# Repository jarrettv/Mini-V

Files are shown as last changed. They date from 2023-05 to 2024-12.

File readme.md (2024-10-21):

# Mini-V

Mini-V is a compact core-xy printer with a build volume of 180mm³ using 2020 extrusions. The printer is designed to maximize print volume with a minimal footprint.

_October 2024 Update: We gathered a ton of great feedback from the Mini-V Group Build in Reno at VICE 2024. We have multiple builders sending in tips and feedback. We also now have full assembly CAD and a build guide available. Enjoy!_

<p align="center">
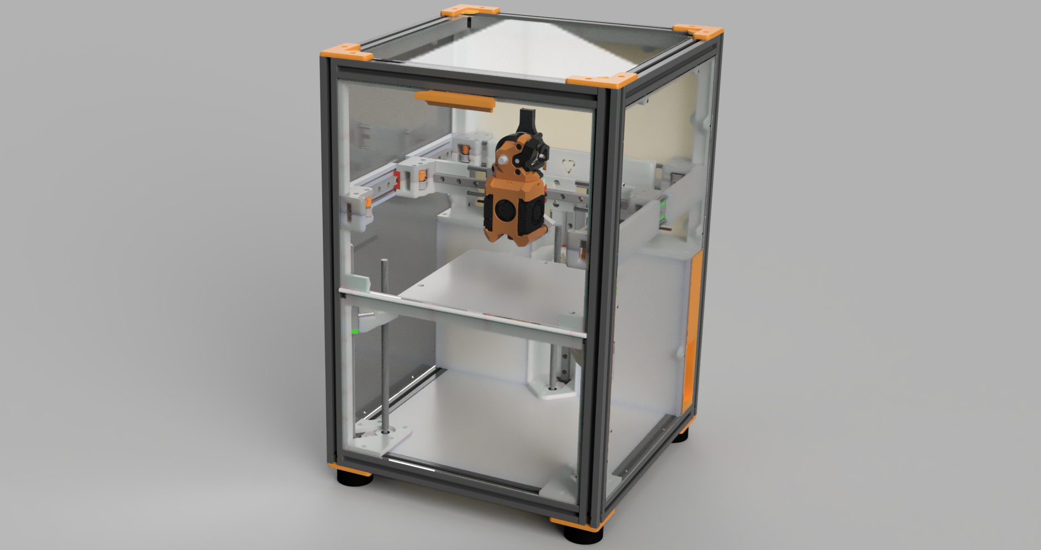
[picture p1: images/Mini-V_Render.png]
  
</p>

- Easy to build 2020 box design ✅
- Super light carbon fiber rod backed X rail ✅
- Sleek flush panels enclosure ✅
- Quick access electronics and host ports ✅
- Fold-down door and easy to remove top panel ✅
- Consistently perfect first layers with Boop ✅
- Automatic bed leveling ✅
- Easy belt tensioning knobs ✅
- Hi-temp dual-mag tri-mount stay-put kinematic bed 😅 ✅
- Magnetic toolhead with dual 4010 part cooling ✅
- Extra headroom for umbilical/PTFE tube ✅
- Dedicated high-voltage and low-voltage areas ✅
- No drag chains ✅
- Mostly M3 SHCS and easy to source hardware ✅
- Toolchanger ready! ↔️

Prototype build log on Discord here: #"jv's Mini-V a custom compact 180³ build using 2020 and CF rods"

- [Specs](./docs/Specs.md) for detailed specifications
- [BOM](./docs/BOM.md) for bill of materials
- [Printing Parts](./docs/PrintingParts.md) for slicer settings and print tips
- [Build Guide](./docs/BuildGuide.md) for step-by-step build instructions
- [Startup Config](./docs/StartupConfig.md) for Klipper configuration and startup routine
- [RepRap History](./docs/RepRapHistory.md) for how this open source printer evolved
- [TODO](./docs/TODO.md) for remaining design areas

## Community Design

Custom magnetic Yavoth toolhead mod with integrated PZ board mount:

<p align="center">
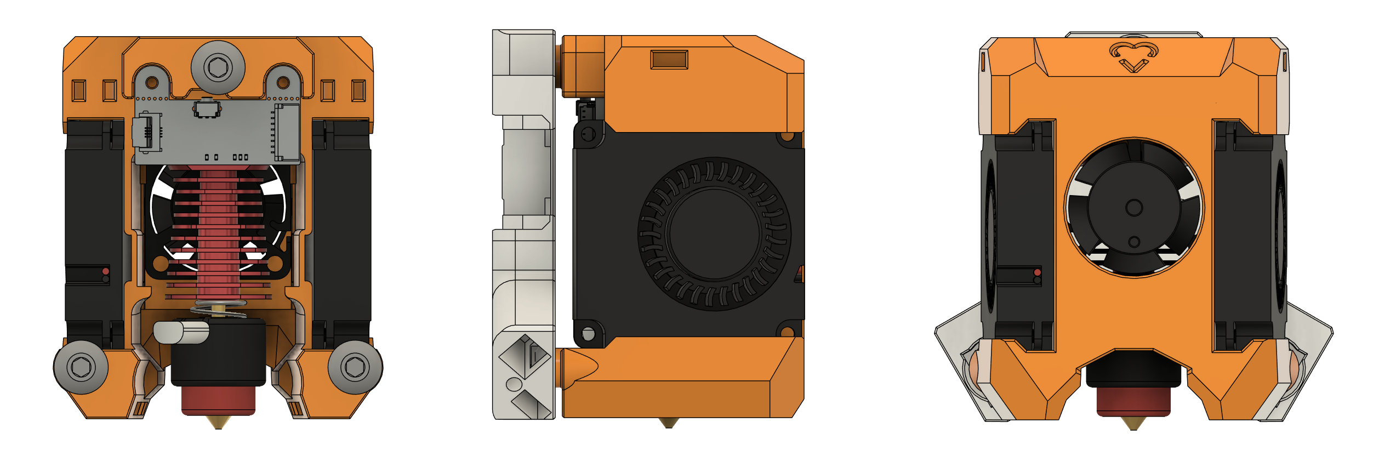
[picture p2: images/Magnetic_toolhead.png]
  
</p>

Although Mini-V is almost a completely custom design, it does utilize the following community designs:

- [Yavoth Toolhead](https://github.com/chirpy2605/voron) by `chirpy2605`
- [Belt Clips](https://github.com/zruncho3d/vampire_bat) by `zruncho3d`
- Inspiration from Voron Trident and is derived from Tiny-T frame dimensions

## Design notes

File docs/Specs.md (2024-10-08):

# Specifications

|  Spec | Desc |
| --- | --- |
| Print Size | 180mm³ ♦️|
| Kinematics | Core-XY |
| Extrusions | 2020 |
| Structure | 5mm Rods |
| Enclosure | Yes, flush |
| Door | Fold-down |
| Bed Leveling | 3-point Automatic |
| Z Accuracy | 0.1µm within a range of 6µm |
| Z Motion | Integrated lead-screws |
| A/B Voltage | 24v or 48v 🔰 |
| A/B Size | NEMA 17 |
| Belts | 2MGT (GT3) |
| Toolhead Board | EBB36 |
| Mainboard | E3EZ |
| Host CPU | Pi CM4 |
| Extruder | G2 |
| Hotend Cooling | 25x10 Axial |
| Part Cooling | Dual 40x10 Blowers |
| Hardware | M3 SHCS 98% |
| Nozzle | High-flow |
| Bed Heater | 300W 120V |
| Rear-clearance | Minimal, angled mains plug |
| Speed Benchy | Very fast |

♦️ Note: all specs are for the default build. Although 180mm build height is possible, with V0 integrated lead screw motors, we will target 170mm.

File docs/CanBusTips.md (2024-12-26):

Please see https://canbus.esoterical.online/

python3 ~/katapult/scripts/flashtool.py -f ~/klipper/out/klipper.bin -d /dev/serial/by-id/usb-katapult_stm32g0b1xx_4A00290012504B4B38383620-if00

mainboard: 183fbc1d936f

provoke3d adxl ampon
make flash FLASH_DEVICE=0483:df11

8d010481812b

python3 ~/katapult/scripts/flashtool.py -i can0 -u 8d010481812b -f ~/klipper/out/klipper.bin

usb-katapult_stm32g0b1xx_4A00290012504B4B38383620-if00

python3 ~/katapult/scripts/flashtool.py -f ~/klipper/out/klipper.bin -d /dev/serial/by-id/usb-katapult_stm32g0b1xx_4A00290012504B4B38383620-if00

21183091201e

python3 ~/katapult/scripts/flashtool.py -i can0 -u 21183091201e -f ~/klipper/out/klipper.bin

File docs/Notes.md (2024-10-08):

Leave deck panel off until back ebays are setup
Belts, start in the rear corner, leave XY inner idler off
  run belts all the way and insert XY inner idler after belts run, turn printer upside down if screws enter from below

When putting on lead screw nuts, move all the way to bottom of z rail before you tighten them down

Y-rail carriages may rub on steel rods, need to add some tolerance for various MGN-9H carriages ✅

Make the foot spacers 2mm taller to account for different brands lead-screw steppers ✅

Move the Z1 bottom motor mount screws to outside so they are more easily accessible for adjustments

Add notches into front Z motor mounts so front feet screws don't interfere  ✅

Add tiny slots to Z motor mounts so there is some play
  Shouldn't be necessary, need more testing results

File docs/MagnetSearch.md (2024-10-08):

# Magnets

Mini-V uses magnets in high-temperature areas which means ordinary magnets are not up to the task. I have over a years worth of print time using <abbr title="Samarium Cobalt">SmCo</abbr>  magnets and they hold up great even with repeated high bed/chamber temp cycles.

Normal neodymium magnets fail after the first couple heat cycles. However, there are high-temp classes:

## Neodymium Temp Classifications
- N	176°F (80°C)	590°F (310°C)
- NM	212°F (100°C)	644°F (340°C)
- NH	248°F (120°C)	644°F (340°C)
- NSH	302°F (150°C)	644°F (340°C) **➡️ These and below would work**
- NUH	356°F (180°C)	662°F (350°C)
- NEH	392°F (200°C)	662°F (350°C)
- NAH	428°F (220°C)	662°F (350°C)

## Bed Magnets

The bed magnets need to hold the bed firmly for the following activities:
* Heating bed to ~110°C for printing
* Pulling off the spring steel sheet
* Moving or turning the printer upside down

### Target dimensions
- 20 mm = .787 inches 3/4
- 10 mm = .4 inches 1/2
- 5 mm = .2 inches 1/8

### Candidates

* 20x10x5mm SmCo Magnets (Found on Ali)
  * No longer available
  * Great size and work fantastic
  * See [bed_Mag_Kinematic_Mount_x3.stl](../parts/bed_Mag_Kinematic_Mount_x3.stl)

* High Temp N42SH Neodymium Magnets 1 in x 1/2 in x 1/4 in Rare Earth Block
  * Oversized but very strong pull
  * See [bed_[a]_Kinematic_Bed_Mount_Neo_SH_Large_x3.stl](../parts/bed_[a]_Kinematic_Bed_Mount_Neo_SH_Large_x3.stl)

* SmCo Magnets 1/2 in x 1/2 in x 1/4 in Samarium Cobalt Block
  * Workable, but doesn't quite seem strong enough
  * See [bed_[a]_Kinematic_Bed_Mount_SmCo_Small_x3.stl](../parts/bed_[a]_Kinematic_Bed_Mount_SmCo_Small_x3.stl)

## Toolhead Magnets

The toolhead magnets need to hold the toolhead firmly for the following activities:
* Printing up to ~270°C and up to 70°C chamber temps
* Sensorless homing
* Fast acceleration printing

### Candidates

* 1/2" x 1/4" x 1/8" Blocks - SmCo - Samarium Cobalt
  * Must double-up for stronger hold
  * See [gantry_X_Carriage_Magnetic_x1.stl](../parts/gantry_X_Carriage_Magnetic_x1.stl)

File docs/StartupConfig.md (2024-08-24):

# Startup and Configuration

Follow klipper docs
Follow Voron Trident docs

TBD Mini-V specific startup and config

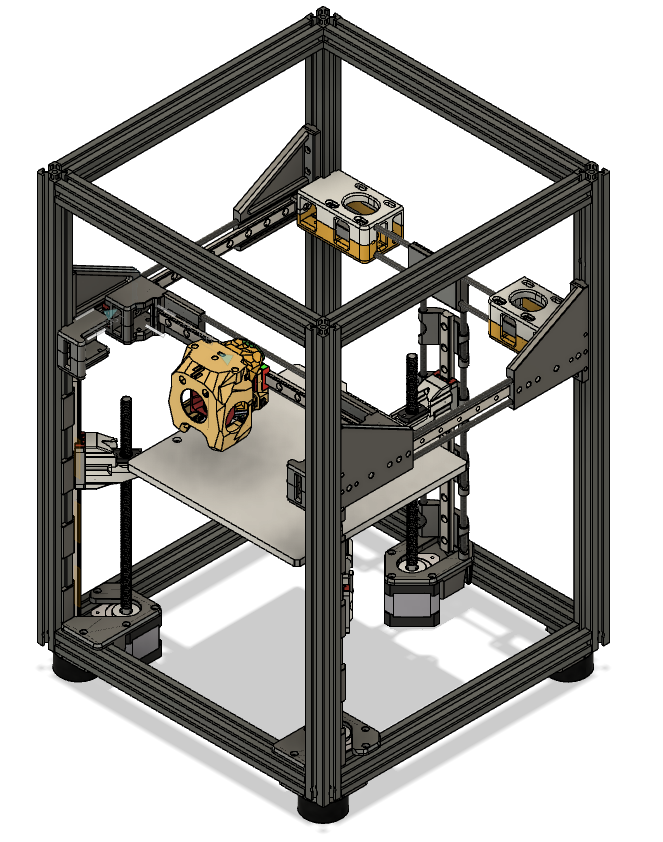
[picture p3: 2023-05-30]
images/concept.png

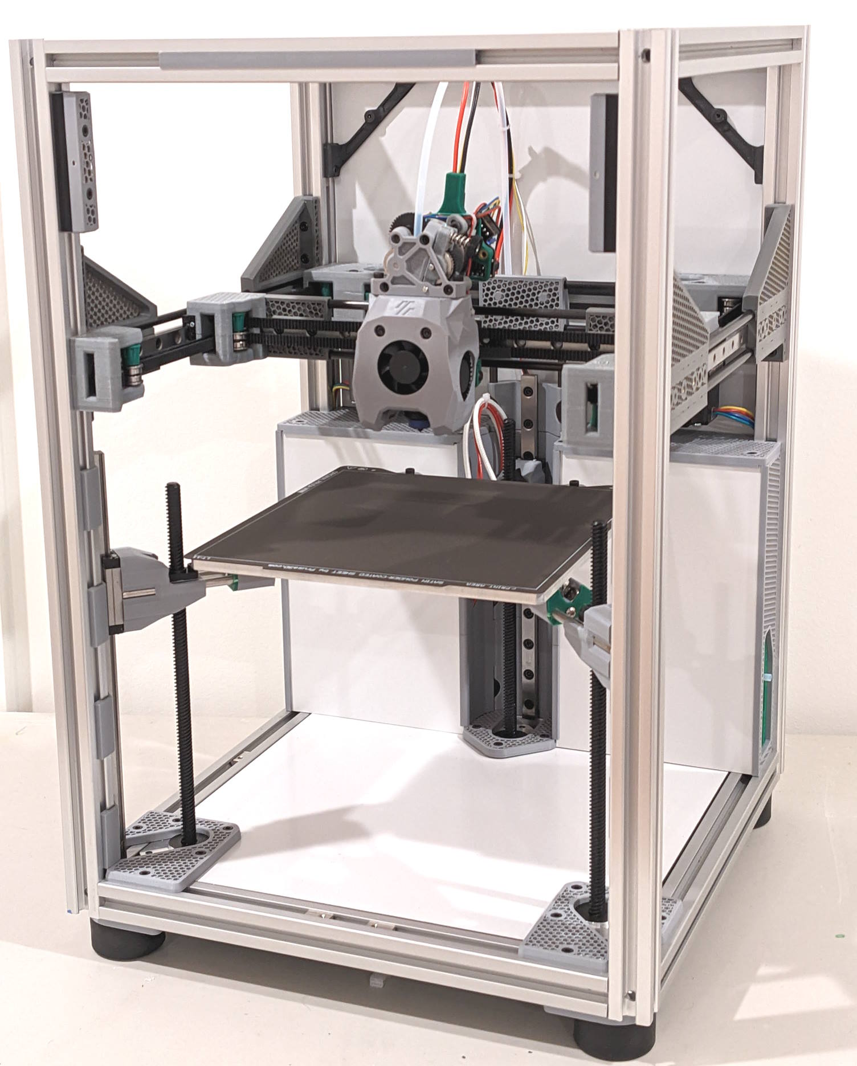
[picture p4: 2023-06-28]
images/Mini-V_prototype_june_2023.jpg

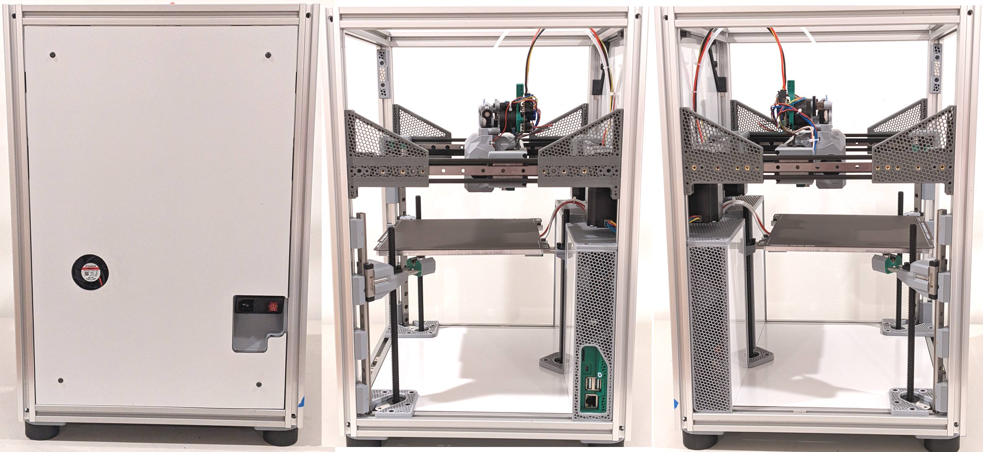
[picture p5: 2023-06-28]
images/Mini-V_back_right_left.jpg

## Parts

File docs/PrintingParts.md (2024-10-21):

# Printing Parts

## Main parts

Many of the main parts are structural so we recommend a filled filament. Although they were specifically designed to be printable with an 0.6mm nozzle, I still recommend a 0.4mm nozzle as the parts require less post-processing. 

| Setting | Value |
| --- | --- |
| Nozzle | 0.6mm or 0.4mm |
| Filament | CF or GF ABS or ASA |
| Infill | 25% (honeycomb) |
| Extrusion width | 0.6mm or 0.4mm |
| Perimeters | 4 |
| Top layers | 5 |
| Bottom layers | 4 |

- [x] bed_Front_Z_Rail_Mount_x4
- [x] bed_Front_Z_Rail_Panel_A_Mount_x2
- [x] bed_Front_Z_Rail_Panel_B_Mount_x2
- [ ] bed_Mag_Kinematic_Mount_x3
- [x] bed_Z0_Motor_Mount_x1
- [x] bed_Z1_Motor_Mount_Rear_x1
- [x] bed_Z1_Rail_Mount_Top_x1
- [x] bed_Z1_Rail_Mount_Wire_Manage_x1
- [x] bed_Z1_Rail_Mount_x3
- [x] bed_Z1_Top_Tensioner_Clamp_Back_x1
- [x] bed_Z1_Top_Tensioner_Clamp_Front_x1
- [x] bed_Z2_Motor_Mount_x1
- [x] bed_Z_Carriage_Mount_x3
- [x] ebay_E3EZ_Mount_x1
- [x] ebay_High_Voltage_Side_x1
- [x] ebay_Low_Voltage_Side_x1
- [x] ebay_Mains_Inlet_Mount_x1
- [ ] ebay_PSU_Mount_x2
- [x] ebay_Top_Cover_High_Voltage_x1
- [x] ebay_Top_Cover_Low_Voltage_x1
- [x] gantry_A_Motor_Mount_Bot_x1
- [x] gantry_A_Motor_Mount_Top_x1
- [x] gantry_A_Motor_Mount_x1
- [x] gantry_B_Motor_Mount_Bot_x1
- [x] gantry_B_Motor_Mount_Top_x1
- [x] gantry_B_Motor_Mount_x1
- [x] gantry_Front_Idler_Bot_Left_x1
- [x] gantry_Front_Idler_Bot_Right_x1
- [x] gantry_Front_Idler_Top_Left_x1
- [x] gantry_Front_Idler_Top_Right_x1
- [x] gantry_XY_Joint_Left_Bot_x1
- [x] gantry_XY_Joint_Left_Top_x1
- [x] gantry_XY_Joint_Right_Bot_x1
- [x] gantry_XY_Joint_Right_Top_x1
- [x] gantry_X_Carriage_Magnetic_x1
- [x] gantry_X_Rail_End_Mount_x2
- [x] gantry_X_Rail_Mid_Mount_x2
- [x] gantry_Y_Rail_Mount_x4
- [x] panels_Clip_Door_Hinge_Latch_Left_x1
- [x] panels_Clip_Door_Hinge_Latch_Right_x1
- [x] panels_Clip_Dual_Mount_Wire_Slot_Right_x1
- [x] panels_Clip_Dual_Mount_Wire_Slot_Left_x1
- [x] panels_Clip_Dual_Mount_x2
- [x] panels_Clip_LED_Stick_A_x2
- [x] panels_Clip_LED_Stick_B_x2
- [ ] panels_Clip_Long_x6
- [x] panels_Clip_Magnet_Door_Latch_Left_x1
- [x] panels_Clip_Magnet_Door_Latch_Right_x1
- [ ] panels_Clip_Short_x2
- [x] panels_Clip_Single_Mount_x8
- [x] panels_Clip_x31
- [x] panels_Front_Door_Bottom_Rest_x2
- [t] panels_Front_Door_Hinge_Lower_Edge_Left_x1
- [t] panels_Front_Door_Hinge_Lower_Edge_Right_x1
- [t] panels_Front_Door_Hinge_Lower_Mid_Left_x1
- [t] panels_Front_Door_Hinge_Lower_Mid_Right_x1
- [t] panels_Front_Door_Hinge_Mid_x3
- [t] panels_Front_Door_Hinge_Upper_Left_x1
- [t] panels_Front_Door_Hinge_Upper_Right_x1

## Panel Clips (feature less)

Any of the clips that don't have special features can be printed with 0.6 nozzle in vase mode for an even better snap-in feel. The following settings have been tested with ABS-GF, YMMV. Depending on your bed and toolhead size, you can print many in a batch using "Complete individual objects" setting.

| Setting | Value |
| --- | --- |
| Nozzle | 0.6mm |
| Filament | ABS or ASA GF |
| Infill | none |
| Extrusion width | 0.85mm forced width |
| Perimeters | 1 *Spiral vase mode |
| Top layers | 0 |
| Bottom layers | 0 |
| Elephant foot comp. | 0 |

- [x] panels_Clip_30mm_x10
- [x] panels_Clip_45mm_x6
- [x] panels_Clip_60mm_x12

## Accent parts

Most of these parts are designed for 0.4mm nozzle. Choose a bright color to make them "pop"! 

> [!CAUTION]
> Filled filaments are ok too but I suggest you print a few tolerance test prints for your bearing stacks.

| Setting | Value |
| --- | --- |
| Nozzle | 0.4mm |
| Filament | ABS or ASA (bright color) |
| Infill | 40% (honeycomb) |
| Extrusion width | 0.4mm |
| Perimeters | 4 |
| Top layers | 5 |
| Bottom layers | 4 |

- [ ] gantry_[a]_Bearing_Stack_Double_x2
- [ ] gantry_[a]_Bearing_Stack_Double_x2_(filled)
- [ ] gantry_[a]_Bearing_Stack_Single_x8
- [ ] gantry_[a]_Bearing_Stack_Single_x8_(filled)
- [ ] gantry_[a]_Bearing_Stack_Washer_x12
- [ ] gantry_[a]_Belt_Clip_x2
- [ ] gantry_[a]_Guidler_Spacer_x2
- [ ] gantry_[a]_Guidler_Washer_x2
- [ ] bed_[a]_Kinematic_Bed_Mount_Neo_SH_Large_x3
- [-] bed_[a]_Kinematic_Bed_Mount_SmCo_Small_x3
- [-] bed_[a]_Mag_Kinematic_Mount_Cover_x3
- [ ] bed_[a]_Z1_Top_Tensioner_Knob_x2
- [ ] ebay_[a]_E3EZ_IO_Shield_x1
- [t] ebay_[a]_Foot_Mount_(LDO)_x4
- [-] ebay_[a]_Foot_Mount_(taller)_x4
- [ ] ebay_[a]_PSU_LED_Mount_x2
- [ ] panels_[a]_Door_Magnetic_Handle_x1
- [t] panels_[a]_Top_Latch_Mount_x4
- [ ] panels_[a]_Top_Latch_Pick_x4
- [x] toolhead_Yavoth_Revo_PZ_Magnetic_Cowl_x1
- [-] toolhead_[a]_Dragon_Burner_V8_Mini-V_x1
- [x] toolhead_[a]_Yavoth_Magnetic_Cowl_x1

## Mesh parts

The parts look solid but you need to print them with your favorite breathable infill. I prefer honeycomb at 25%.

| Setting | Value |
| --- | --- |
| Nozzle | 0.4mm |
| Filament | ABS or ASA (bright color) |
| Infill | 25% (honeycomb) |
| Extrusion width | 0.4mm |
| Perimeters | 4 |
| Top layers | 0 for first 3mm |
| Bottom layers | 0 for first 3mm |

- [ ] ebay_[a]_High_Voltage_Mesh_x1
- [ ] ebay_[a]_Low_Voltage_Mesh_x1

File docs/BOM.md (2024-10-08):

| Quantity | Part | For | Sources |
| --- | --- | --- | --- |
| 4 | HFSB5-2020-440-LCP-RCP | Corners | Misumi, Dllpdf, Amazon (DIY) |
| 8 | HFSB5-2020-270-TPW | Tops/bottoms | Misumi, Dllpdf, Amazon (DIY) |
| 6 | MGN9 Linear Rail 220mm length | Motion | Fabreeko, Ali |
| 2 | GATES GT3 6mm open belt ~150cm | Motion | Filastruder |
| 4 | F623-RS Bearings | Motion | Filastruder |
| 24 | F695 Bearings | Motion | Filastruder |
| 2 | NEMA 17 stepper motors | A/B motors | SteppersOnline, LDO |
| 3 | NEMA 17 steppers w/ 200mm lead screw | Z motors | SteppersOnline, LDO |
| 3 | 5mm Ø Carbon Fiber Rod 280mm length | X-rail backer | Amazon, Ali |
| 1 | 5mm Ø Carbon Fiber Rod 269mm length | Door hinge | Amazon, Ali |
| 4 | 5mm Ø Steel Rod 269mm length | Y-rail backer | Amazon, Ali |
| 4 | 5mm Ø Steel Rod 279mm length | Rear backer | Amazon, Ali |
| 6 | 5mm Ø Steel Rod 80mm length | Z kinematics | Amazon, Ali |
| 3 | Steel balls 10mm M4 threaded (magnetic) | Z kinematics | Filastruder, Amazon, Ali |
| 6 | High-temp magnets 20x10x5mm (SaCo) | Z kinematics | Specialty, Ali |
| 3 | M4x10 low-profile SHCS | Z kinematics | McMaster, BoltDepot, Ali |
| 6 | M5 washers | Z kinematics | McMaster, BoltDepot, Ali |
| 6 | High-temp magnets 1x0.5x0.25in (Neo SH) | Z kinematics | Specialty, Ali |
| 6 | High-temp magnets 0.5x0.25x0.125in (SaCo) | Magnetic toolhead | Specialty, Ali |
| 1 | 180mm² or 185mm² MIC6 bed | Bed | Mandala Rose Works |
| 1 | 180mm² PEI flex build plate | Bed | Prusa, DFH, KB3D, Fabreeko, West3D |
| 1 | 150mm² 300w AC heating pad | Bed | KB3D, Fabreeko, DFH |
| 1 | Galileo2 recommended | Extruder | DFH, KB3D, Fabreeko, West3D, Ali |
| 1 | E3D Revo PZ High-flow recommended | Hotend | DFH, KB3D, Fabreeko, West3D, Ali |
| 2 | 4010 24V blower fan | Part cooling | DFH, Fabreeko, West3D, Ali |
| 1 | 2510 24V blower fan | Hotend cooling | Amazon, DFH, Fabreeko, West3D, Ali |
| 4 | Rubber amplifier feet | | Amazon, Ali |
| 1 | BTT E3EZ 5 stepper control board | Electronics | BIQU, Amazon, Ali |
| 1 | BTT EBB36 CAN toolhead board | Electronics | BIQU, Amazon, Ali |
| 3 | BTT EZ Driver EZ2209 (2 extra for 24v) | Electronics | BIQU, Amazon, Ali |
| 2 | BTT EZ Driver EZ5160 RGB (for 48v) | Electronics | BIQU, Amazon, Ali |
| 1 | SSR Relay | Electronics | Amazon, Ali |
| 2 | Daylight on a stick | Electronics | DFH, KB3D, Fabreeko, West3D |
| 2 | M4 OD, M3 ID 30mm long steel tubes | Belt clips | DFH, Amazon, McMaster, Ali |
| 2 | GT2 20T Pulley | Hardware | Amazon, Filastruder, DFH |
| 4 | M4 thumb screws | Hardware | McMaster, BoltDepot, Ali |
| 2 | M5x40 hex head bolts | Hardware | McMaster, BoltDepot, Ali |
| 2 | M5 nuts | Hardware | McMaster, BoltDepot, Ali |
| 17 | M5x16 BHCS | Hardware | McMaster, BoltDepot, Ali |
| 2 | M3x10 BHCS | Hardware | McMaster, BoltDepot, Ali |
| ~150 | M3x4x5 Heatset brass inserts | Hardware | McMaster, BoltDepot, Ali |
| 1 | 3mm Clear Top Panel 269x269 | Panels | Hardware store, Amazon, Plastic |
| 2 | 3mm Clear side Panel 399x269 | Panels | Hardware store, Amazon, Plastic |
| 1 | 3mm Clear Front Door Panel XXXx269 | Panels | Hardware store, Amazon, Plastic |
| 1 | 3mm Clear Front Bottom Panel XXXx269 | Panels | Hardware store, Amazon, Plastic |
| 1 | 3mm ACM Rear Panel 399x269 | Panels | Hardware store, Amazon, Plastic |
| 1 | 3mm ACM Deck Panel 269x269 | Panels | Hardware store, Amazon, Plastic |
| 2 | 3mm ACM Mid Panel 120x200 | Panels | Hardware store, Amazon, Plastic |

Mostly M3x6, M3x8, M3x10, M3x20, M3x30, M3x35 SHCS

TBD M3 SHCS counts
TBD M3 FHCS counts
TBD M5 BHCS counts
TBD wires / lengths

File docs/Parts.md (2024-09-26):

| Part | Wt. | Qty | Main | Accent |
|---|---|-----|---|---|
| bed_Z0/Z2_Motor_Mount | 16.0g  | 2 | 32.0g  | |
| bed_Z1_Motor_Mount | 18.5g  | 1 | 18.5g  | |
| gantry_Y_Rail_Mount | 18.0g  | 4 | 72.0g  | |
| gantry_Front_Idler_Top / Bot |  6.0g  | 4 | 24.0g  | |
| gantry_AB_Idler_Mount_Top / Bot |  8.0g  | 4 | 32.0g  | |
| gantry_AB_Motor_Mount | 14.0g  | 2 | 28.0g  | |
| bed_Top_Tensioner_Clamp_Back | 12.0g  | 1 | 12.0g  | |
| bed_Top_Tensioner_Clamp_Front |  8.5g  | 1 |  8.5g  | |
| gantry_XY_Joint_Top / Bot |  6.5g  | 4 | 26.0g  | |
| gantry_XY_Joint_X_Rail_Mount |  7.0g  | 2 | 14.0g  | |
| gantry_X_Rail_Mid_Mount |  5.5g  | 2 | 11.0g  | |
| bed_Front_Z_Rail_Mount |  4.0g  | 6 | 24.0g  | |
| bed_Front_Z_Rail_Panel_Low/Up_Mount |  4.0g  | 4 | 16.0g  | |
| ebay_High/Low_Voltage_Side | 25.0g  | 2 | 50.0g  | |
| ebay_Mains_Inlet_Mount | 28.0g  | 1 | 28.0g  | |

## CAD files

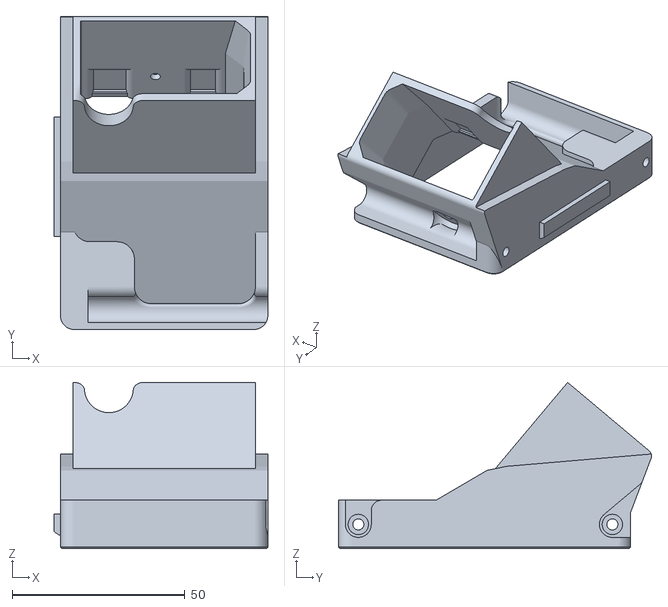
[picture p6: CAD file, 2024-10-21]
parts/ebay_Mains_Inlet_Mount_x1.stl
61.8 x 90.6 x 48.1

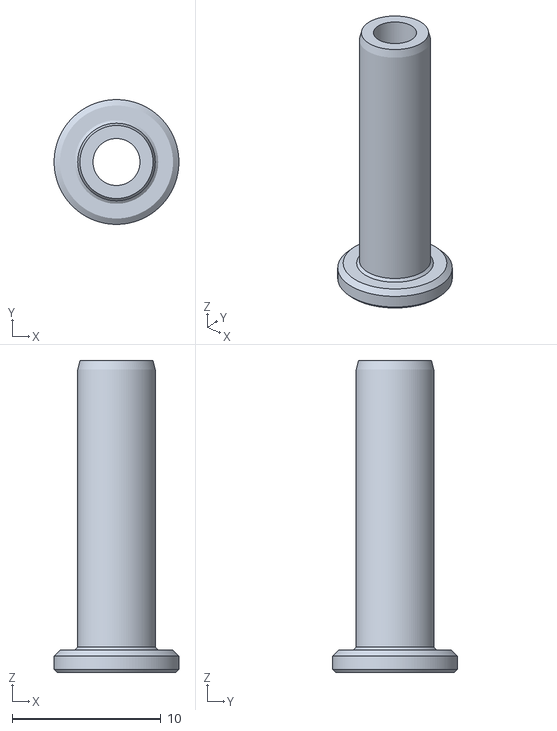
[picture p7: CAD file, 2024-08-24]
parts/gantry_[a]_Bearing_Stack_Full_x2.stl
8.40 x 8.40 x 21.0

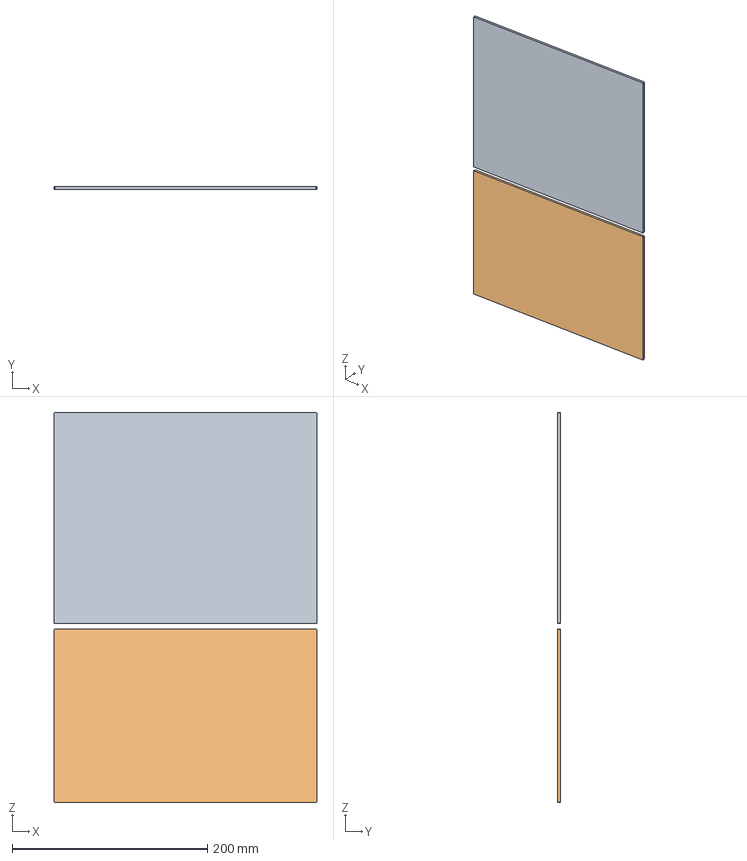
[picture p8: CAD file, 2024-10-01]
panels/Front_Door_Panels_Clear_v5.step
269.0 x 3.00 x 399.0 mm

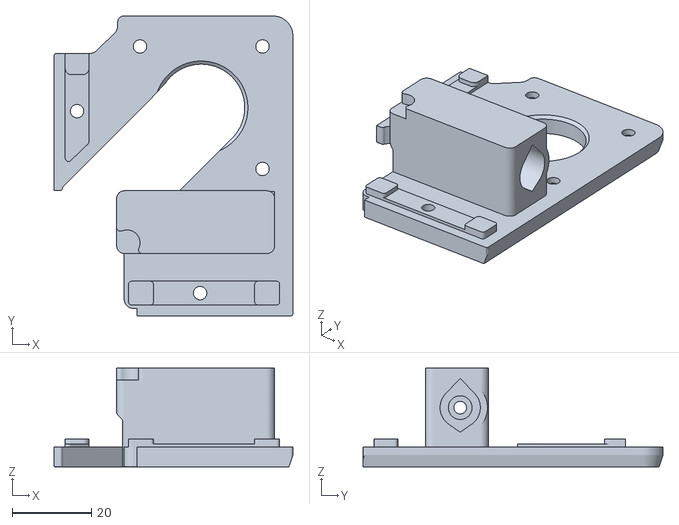
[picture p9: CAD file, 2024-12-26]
parts/bed_Z2_Motor_Mount_x1.stl
60.4 x 75.9 x 25.0

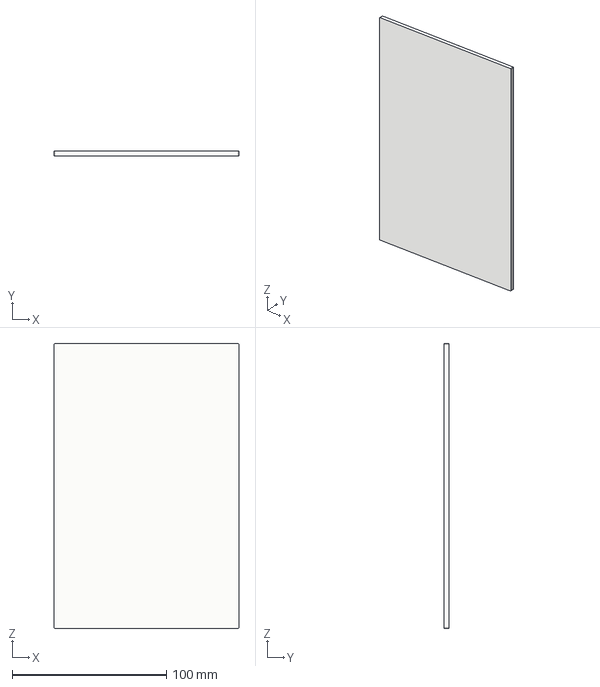
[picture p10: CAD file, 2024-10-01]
panels/Mid_Ebay_Panel_ACM_v2.step
120.0 x 3.00 x 185.0 mm

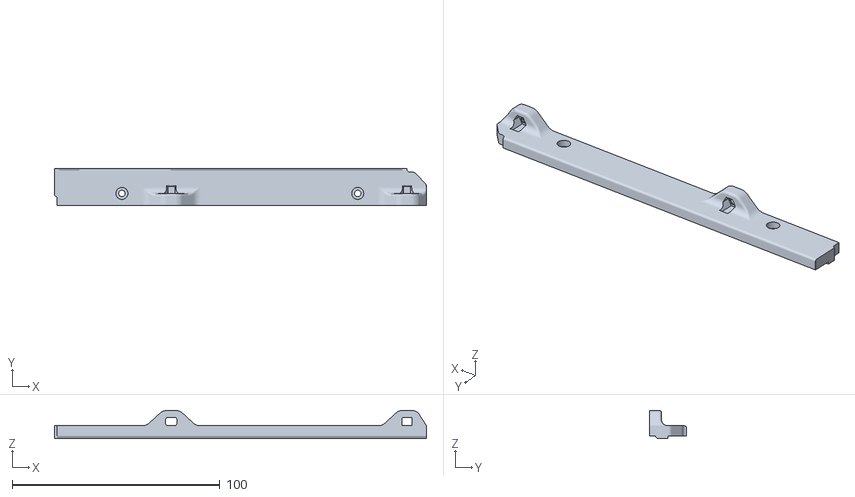
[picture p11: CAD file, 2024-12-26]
parts/panels_Side_Panel_Mag_Mount_Bot_Right_x1.stl
179.0 x 17.8 x 13.6

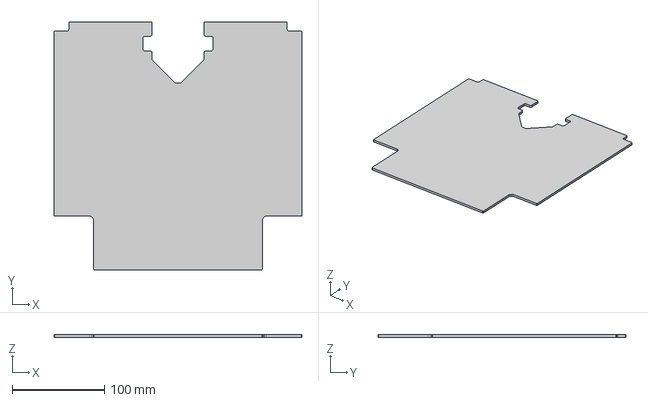
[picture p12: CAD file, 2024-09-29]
panels/Deck_Panel_ACM_v4.step
269.0 x 269.0 x 3.00 mm

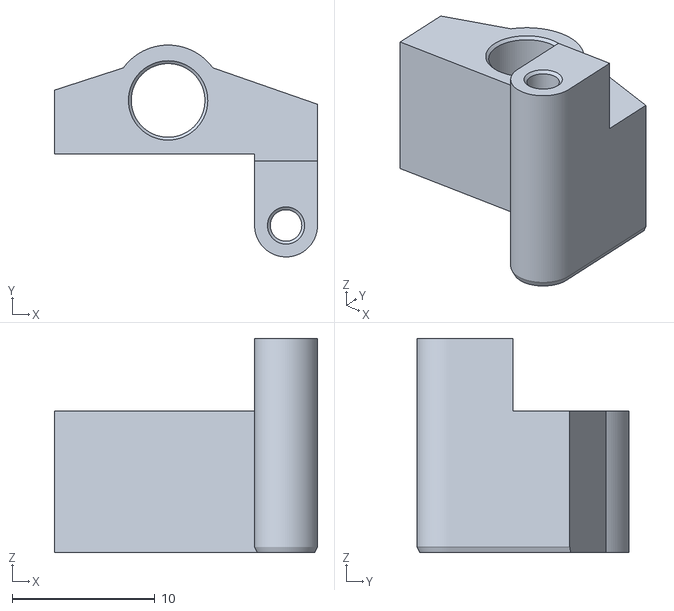
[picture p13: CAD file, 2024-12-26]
parts/panels_Front_Door_Hinge_Lower_Edge_Left_x1.stl
18.4 x 14.8 x 15.0

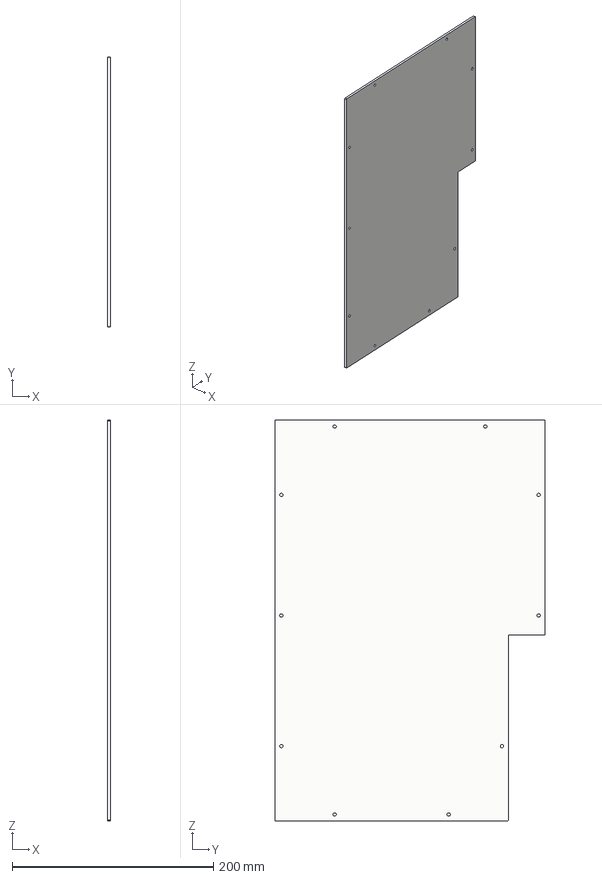
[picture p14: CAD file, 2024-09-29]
panels/Side_Panels_Clear_v3.step
3.00 x 269.0 x 399.0 mm

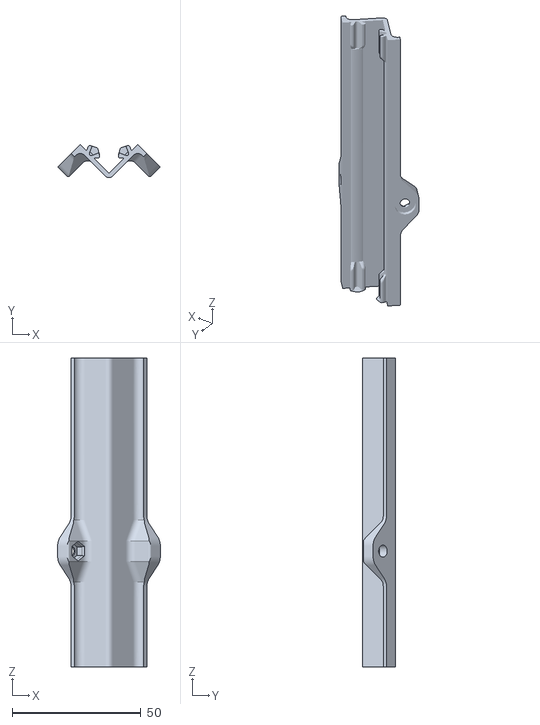
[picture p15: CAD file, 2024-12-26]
parts/panels_Clip_Upper_Rear_Left_x1.stl
39.9 x 13.0 x 120.0

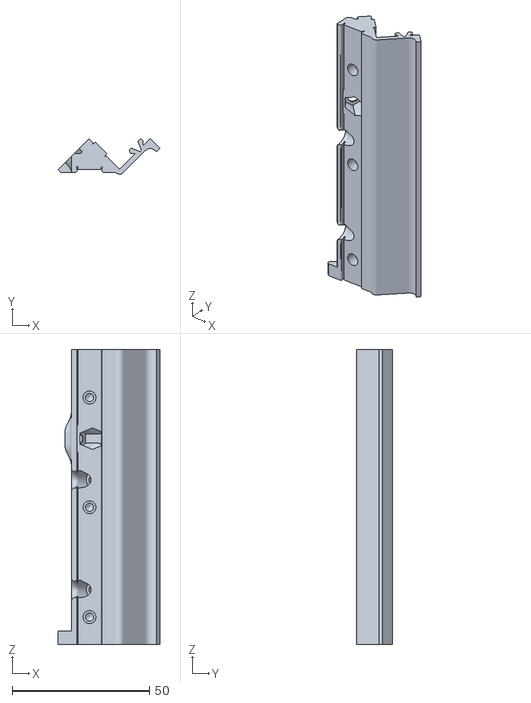
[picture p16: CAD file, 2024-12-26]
parts/bed_Front_Z_Rail_Mount_Right_Bot_x1.stl
37.1 x 13.0 x 107.5

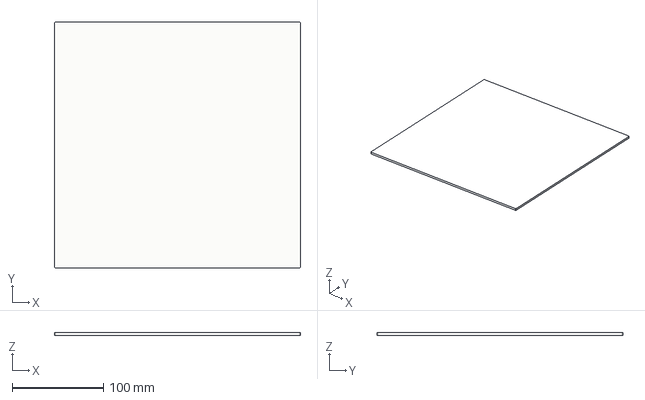
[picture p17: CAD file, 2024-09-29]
panels/Top_Panel_Clear_v1.step
269.0 x 269.0 x 3.00 mm

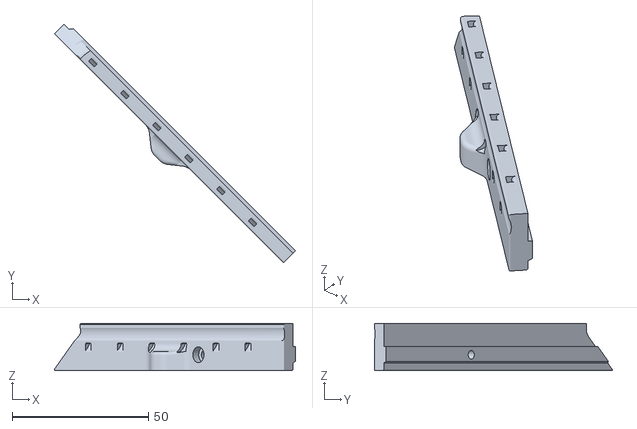
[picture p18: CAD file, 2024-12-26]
parts/panels_Rear_Panel_Bottom_Mount_Right_x1.stl
88.5 x 87.4 x 17.3

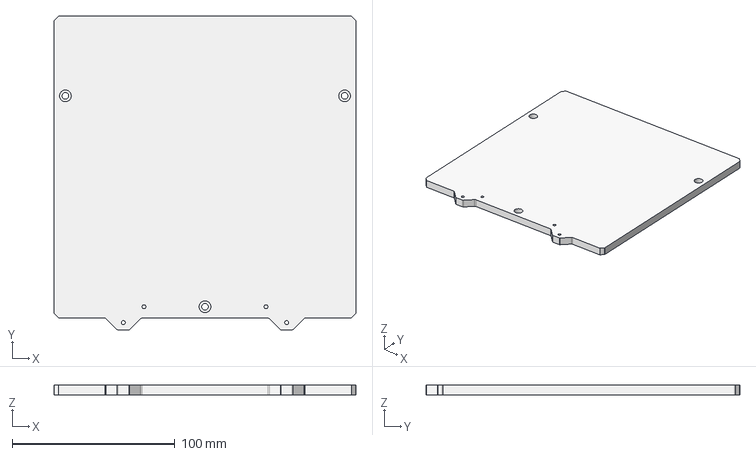
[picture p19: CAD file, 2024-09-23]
panels/185_Mini-V_MIC-6_Bed_v3.step
185.6 x 192.8 x 6.35 mm

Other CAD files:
panels/Back_Panel_ACM_or_Clear_v3.step
parts/panels_Clip_40mm_x6.stl
parts/panels_Clip_Upper_Rear_Right_x1.stl
parts/bed_Front_Z_Rail_Mount_Right_Top_x1.stl
panels/Deck_Panel_ACM_v1.step
parts/bed_Front_Z_Rail_Mount_Left_Bot_x1.stl
parts/bed_Front_Z_Rail_Mount_Left_Top_x1.stl
parts/bed_Front_Z_Rail_Mount_x4.stl
parts/bed_Front_Z_Rail_Panel_A_Mount_x2.stl
parts/bed_Front_Z_Rail_Panel_B_Mount_x2.stl
parts/bed_Mag_Kinematic_Mount_x3.stl
parts/bed_Z0_Motor_Mount_x1.stl
parts/bed_Z1_Motor_Mount_Rear_x1.stl
parts/bed_Z1_Rail_Mount_Bot_x1.stl
parts/bed_Z1_Rail_Mount_Top_x1.stl
parts/bed_Z1_Rail_Mount_Wire_Manage_x1.stl
parts/bed_Z1_Rail_Mount_x3.stl
parts/bed_Z1_Top_Tensioner_Clamp_Back_x1.stl
parts/bed_Z1_Top_Tensioner_Clamp_Front_x1.stl
parts/bed_Z_Carriage_Mount_x3.stl
parts/bed_[a]_Kinematic_Bed_Mount_Neo_SH_Large_x3.stl
parts/bed_[a]_Kinematic_Bed_Mount_SmCo_Small_x3.stl
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

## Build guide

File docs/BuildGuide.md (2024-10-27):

# Build Steps for Mini-V

> [!CAUTION]
> This build guide is a work-in-progress

## General Tips

- Use an ultra flat surface for assembly of frame
- Take a file or flattening stone to all mating surfaces, including all clips
- Panel clips should be snapped in diagonally towards the extrusion

## Gather Hardware

See [BOM](./docs/BOM) for Bill of Materials

## Print Parts

See [Printing Parts](./docs/PrintingParts)

## Heat Sets

- Grab some coffee, I hope you like putting in heat sets as there are many

> [!Tip]  
> You can build the left side of the printer, then the right side, or build them in parallel

## 🔁 Build left side

- Assemble 2 uprights and the bottom extrusion using blind joints M5x16 (2)
  - (optional) Bottom of bottom extrusion will need (2) T-nuts
  - You should have a U shape

<p align="center">
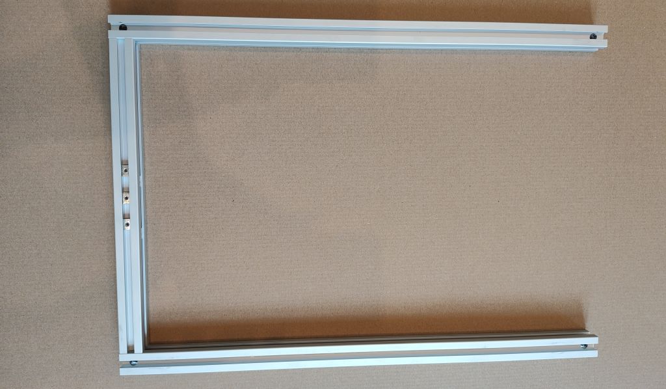
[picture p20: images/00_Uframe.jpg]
  
</p>

### Building Z0 axis

- Add the Z0 motor mount using a M3x30 (1) side and M3x8 (1) screw on top
  - Note: leave these screws slightly loose until the final frame tighten
- Loosely mount Z-rail clips using M3x10 (4)
  - Order from bottom up
    - bed_Front_Z_Rail_Mount, M3x10
    - panels_Clip
    - bed_Front_Z_Rail_Mount_B_Mount (lower), M3x10
    - panels_Clip
    - bed_Front_Z_Rail_Mount, M3x10
    - panels_Clip_Door_Hinge_Latch_Left, M3x8
    - bed_Front_Z_Rail_Mount_A_Mount (upper), M3x10

<p align="center">
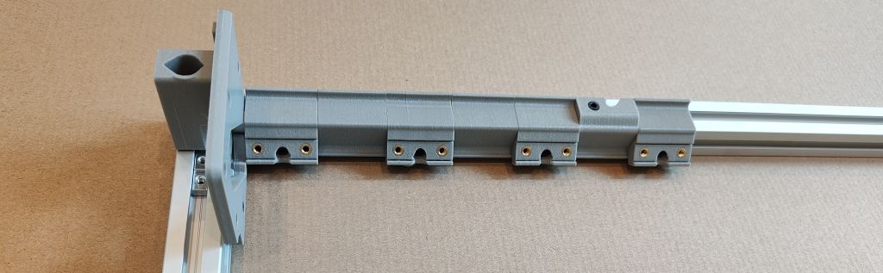
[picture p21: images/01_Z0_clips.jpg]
  
</p>

- Add the z-rail to clips using M3x6 (8)
  - Note: don't tighten down until all screws are in
  - Note: add your clip so carriage doesn't fall out when flipping upside down
- Tighten down Z-rail clips using ball end hex
  - Note: the top clip should line-up or you may need to adjust the clips

<p align="center">
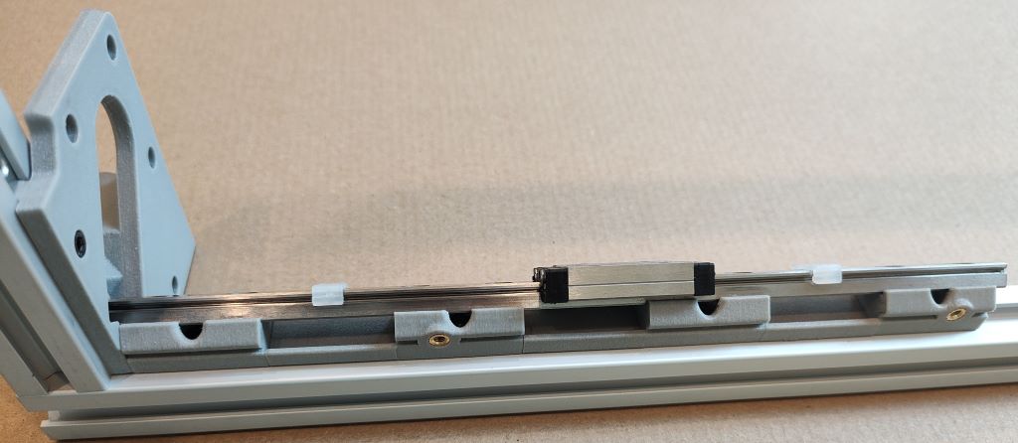
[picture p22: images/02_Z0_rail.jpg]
  
</p>

### Rear E-bay mount (low voltage)

- Note: leave these screws for the ebay mount loose until later, otherwise it might tweak the frame
- Add T-nuts to high-voltage ebay part using M3x10 (1) side middle and M3x6 (1) side top

<p align="center">
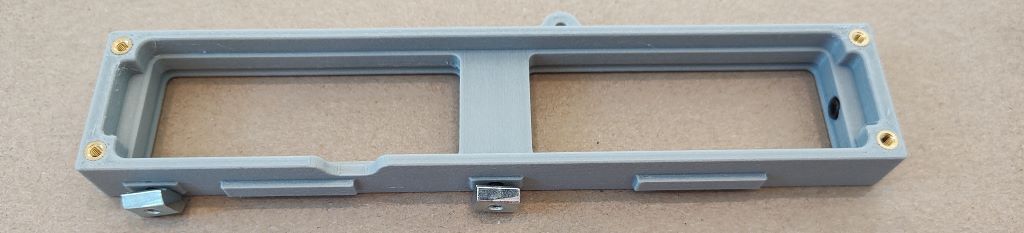
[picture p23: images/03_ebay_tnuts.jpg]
  
</p>

- Roll-in a bottom T-nut in position then slide on ebay part and fasten bottom with M3x8 (1)

### Y Rail mount

- Slide 269mm (2) steel rods into Y-rail mount (2)
  - Note: check the length is not longer than 270

<p align="center">
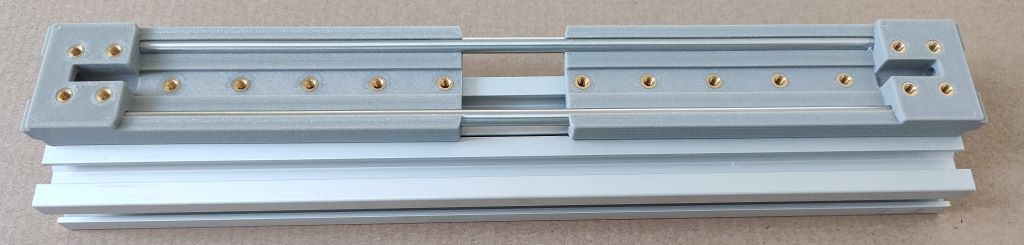
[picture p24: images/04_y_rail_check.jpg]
  
</p>

- Fasten the Y-rail using M3x6 (10) to get proper spacing
  - Note: your Y-rail needs to be cut precisely for this design
- Add T-nuts to each using M3x10 (2) then slide-in between extrusions

> [!CAUTION]
> The following steps requires precise measurements, so take your time

- Use calipers and set to 140mm from very top to top of mount
  - Note: you should see 245mm from lower extrusion to bottom of mount
  - TODO: Add diagram
- Tighten down Y-rail mount on both sides

<p align="center">
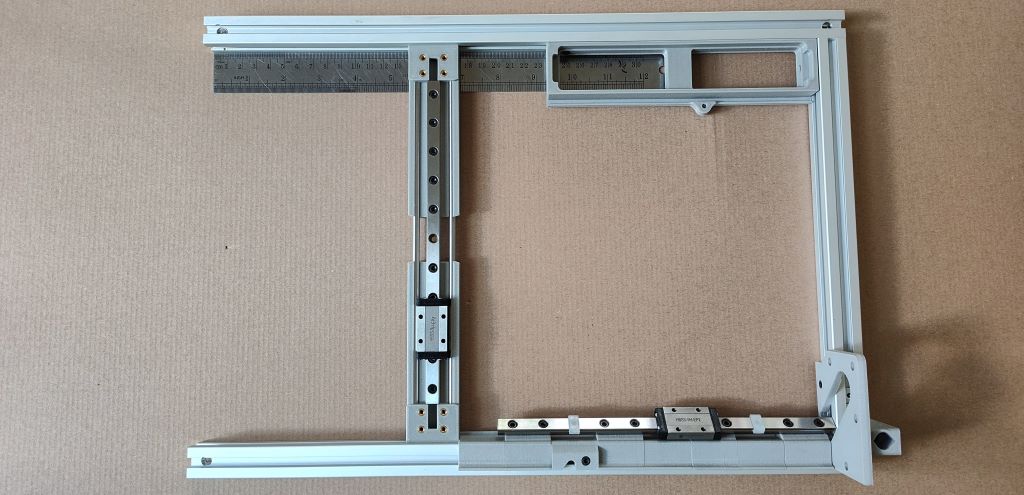
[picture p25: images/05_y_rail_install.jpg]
  
</p>

### Front and rear idlers

- Flatten mating surfaces and screw together front idler using M3x20 (1)
  - Screw front idler to front using M3x8 (4)

<p align="center">
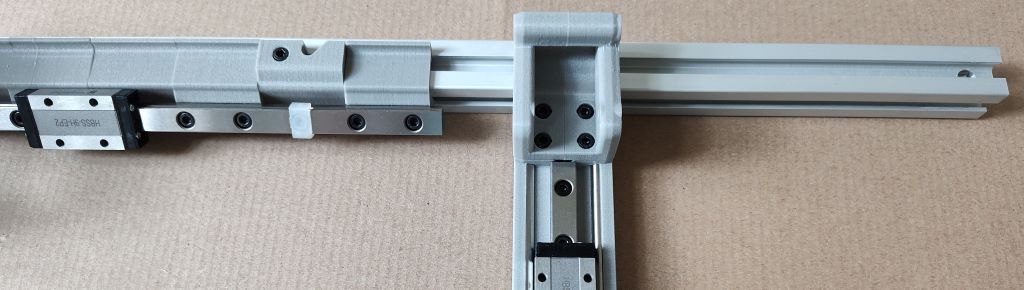
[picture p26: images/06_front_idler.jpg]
  
</p>

- Flatten mating surfaces and screw together the motor idler using M3x20 (2)
  - Screw motor idler to rear using M3x8 (4)

<p align="center">
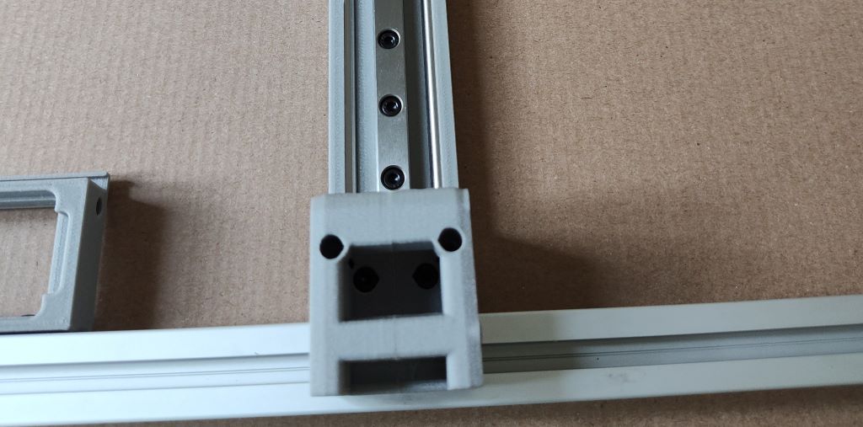
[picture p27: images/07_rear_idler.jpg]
  
</p>

> [!IMPORTANT]  
> The front and rear idlers add rigidity by clamping around the extrusion

<p align="center">
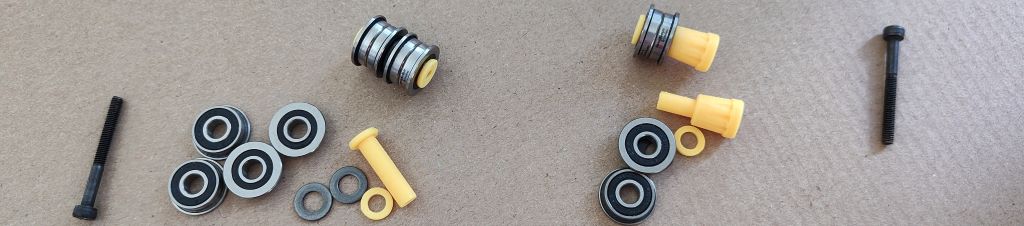
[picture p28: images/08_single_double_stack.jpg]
  
</p>

- Build a single stack bearing using F695 (2) and the plastic washer/clip should pop on the top

  - Add the single stack bearing using M3x30 (1) to the front idler

- Build a double stack bearing using F695 (4), M5 washers (2) and the plastic washer clip will pop on top keeping everything together

  - Add the double stack bearing using M3x30 to the rear motor idler back corner

- Assemble the guilder with the F623-RS (2) bearings in place and use M3x30 (1) screw
- Note: there is a mini plastic washer for the guilder

<p align="center">
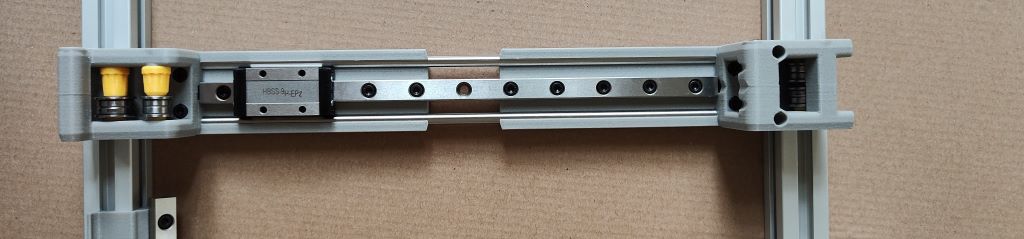
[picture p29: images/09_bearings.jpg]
  
</p>

### XY Joint

- Flatten mating surfaces and screw together the XY Joint using M3x20 (1)
- Screw XY Joint onto Y Rail using M3x6 (4) FHCS
  - Note: you'll need a 2mm ball-end hex driver for the front two screws
- Build a single stack bearing using F695 (2) and the plastic washer/clip should pop on the top
  - Add the single stack bearing using M3x30 (1) to the front idler
  - Note: it should be in opposite orientation of other single stacks

<p align="center">
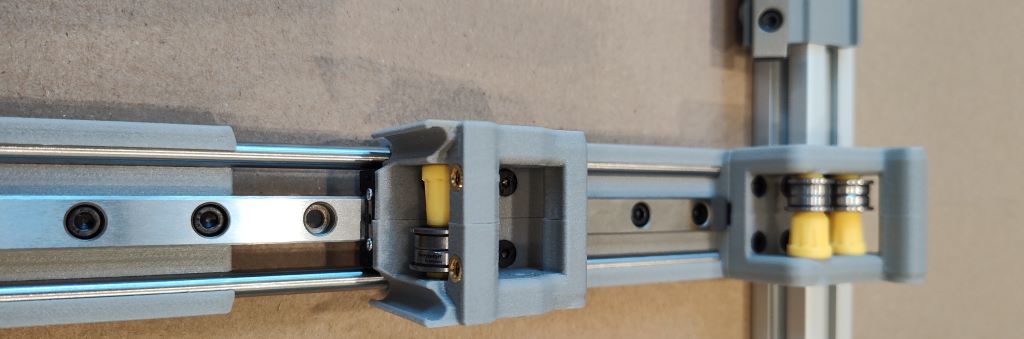
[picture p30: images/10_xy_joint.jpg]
  
</p>

### Add top extrusion

- Add the top extrusion using the blind joints M5x16 (2)
  - (optional) Top extrusion will need (2) T-nuts

<p align="center">
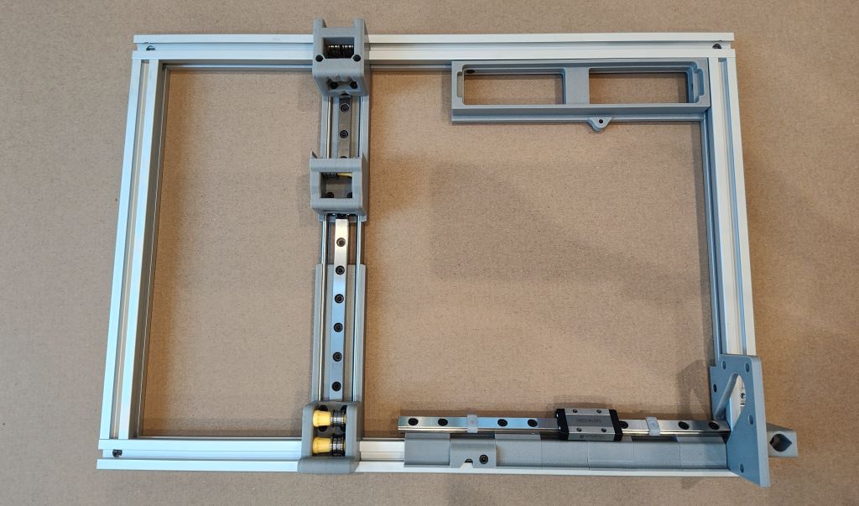
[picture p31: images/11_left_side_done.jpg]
  
</p>

## 🔁 Build right side

- Repeat all left side steps but mirror everything (Z2 motor mount)

<p align="center">
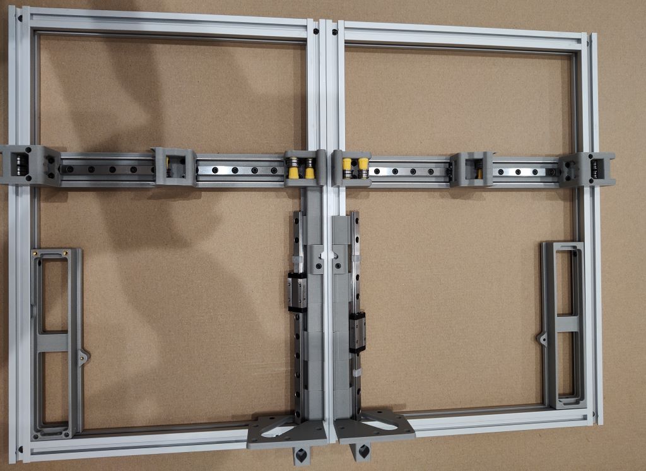
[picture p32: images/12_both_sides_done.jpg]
  
</p>

> [!CAUTION]
> There is a small error in the image above where right side has guilder in wrong spot

## Join sides and finish frame

- Slide motor mounts onto rear 279mm steel rods (2)
- Bring the two sides together by sliding rods into motor idler and on each side

<p align="center">
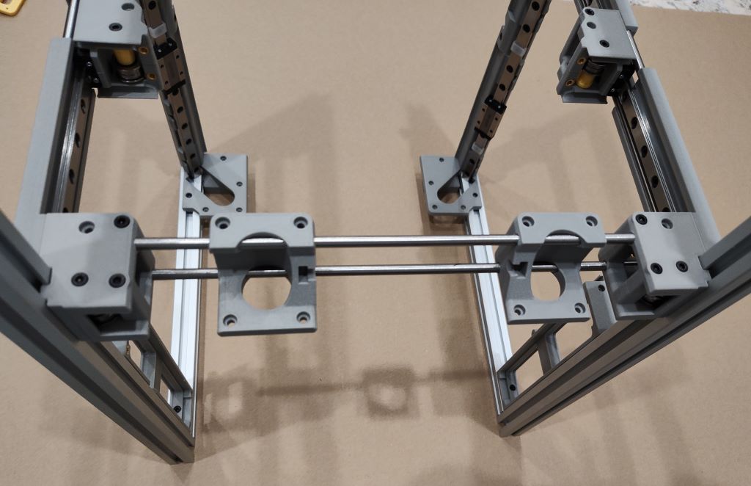
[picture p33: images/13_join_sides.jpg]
  
</p>

- Finish the frame on a flat surface using blind joints and M5x16 (8)
  - Note: ensure frame is square
  - Tighten all the screws you left loose
  - Congrats, it is starting to look like a printer

<p align="center">
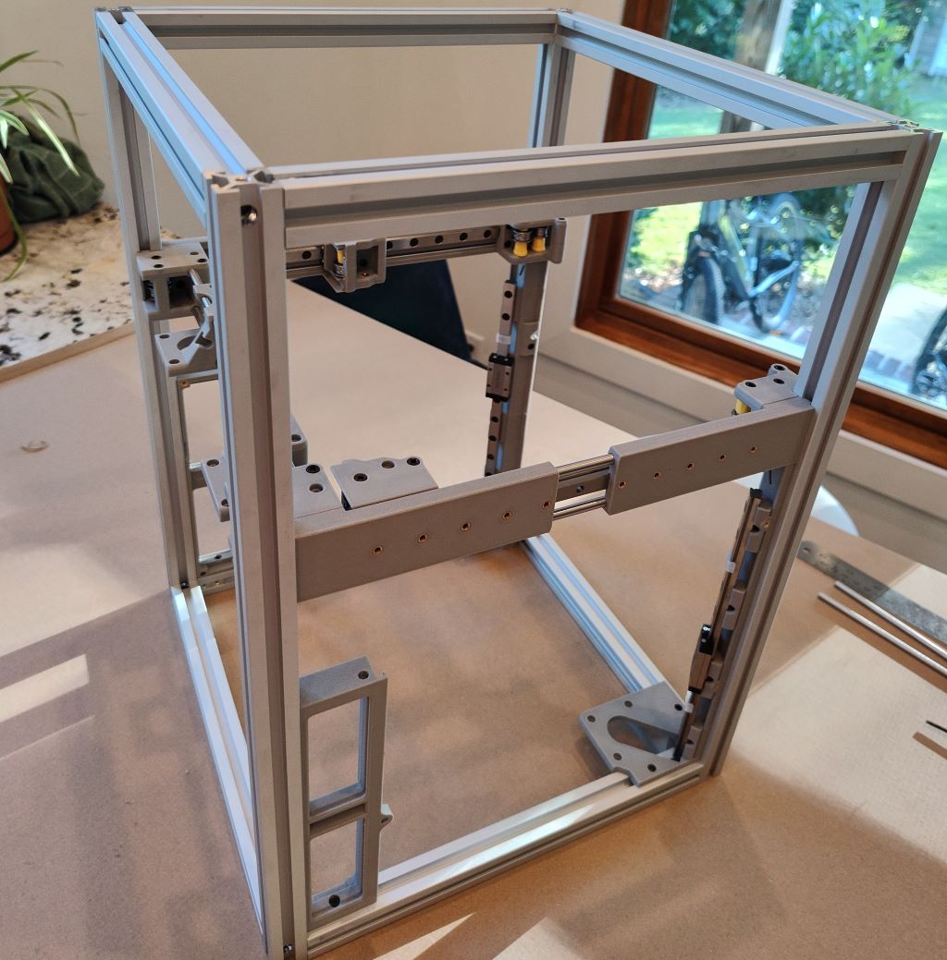
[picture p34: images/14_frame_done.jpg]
  
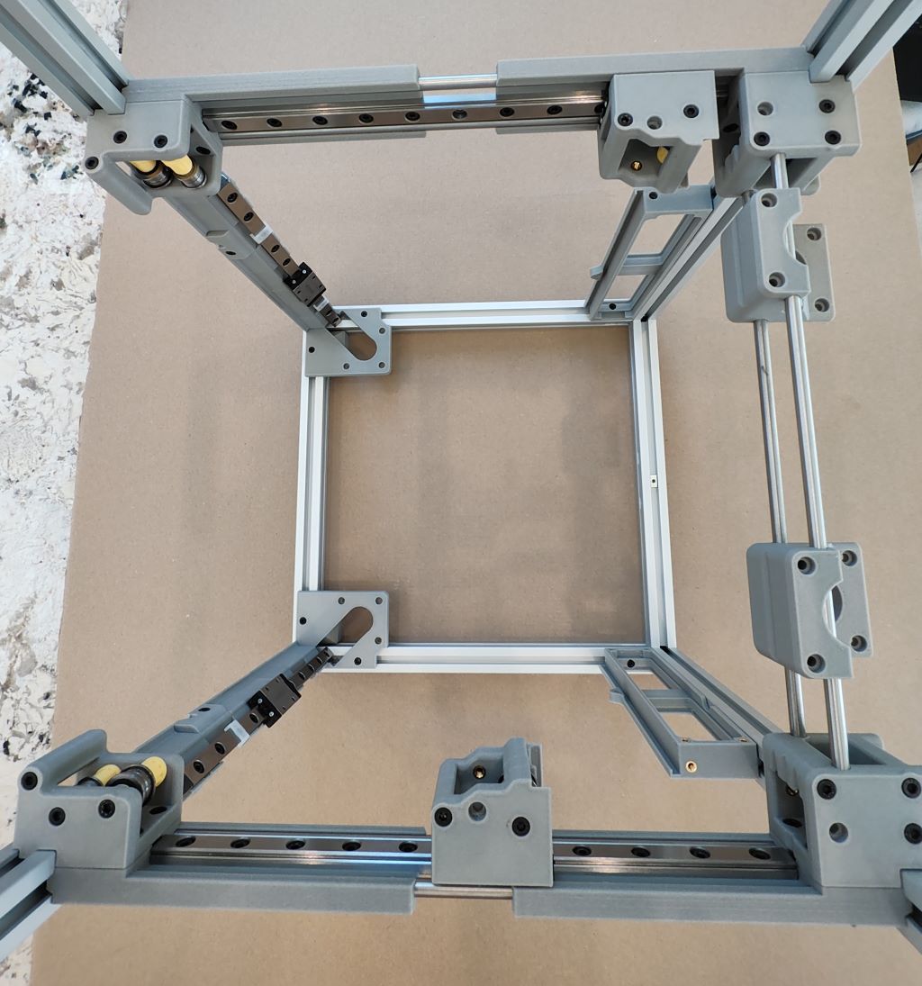
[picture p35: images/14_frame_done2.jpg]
  
</p>

## Feet

- Add all four foot mounts using M3x6 (8) for LDO or M3x8 for taller foot mounts
- Each foot requires a M4 thumbscrew (4) and M3x16 (4) for LDO or M3x20 for taller foot mounts

<p align="center">
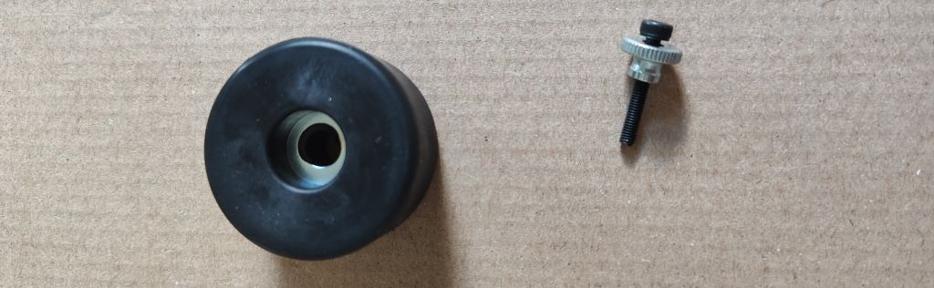
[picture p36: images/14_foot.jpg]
  
</p>

- There is an arc feature on the part to help you align each foot into the correct spot

<p align="center">
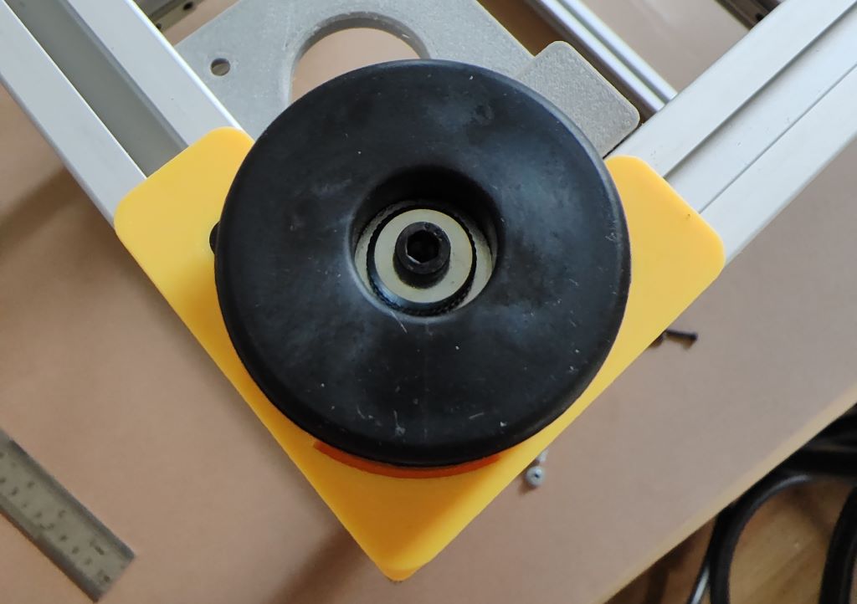
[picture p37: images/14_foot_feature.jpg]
  
</p>

- Add the matching four top panel latches using M3x6 (8)

> [!Tip]  
> Your surface is now protected from scratches by your frame

## X-Rail

- Build the X-Rail backer using 280mm carbon rods (2)
- Mount the X-Rail (choose your best rail) using M3x8 (8)
  - Note: make sure you center things before screwing to the XY Joints

<p align="center">
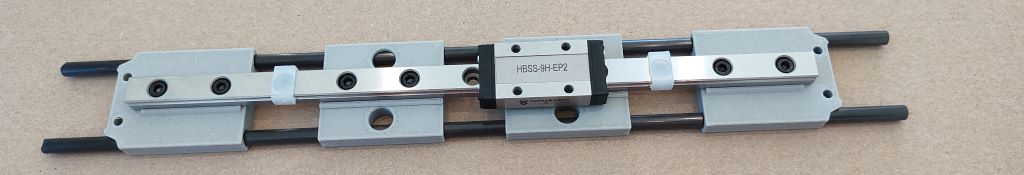
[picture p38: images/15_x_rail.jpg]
  
</p>

- Screw X-Rail Backer to XY-Joints using M3x8 (4)

<p align="center">
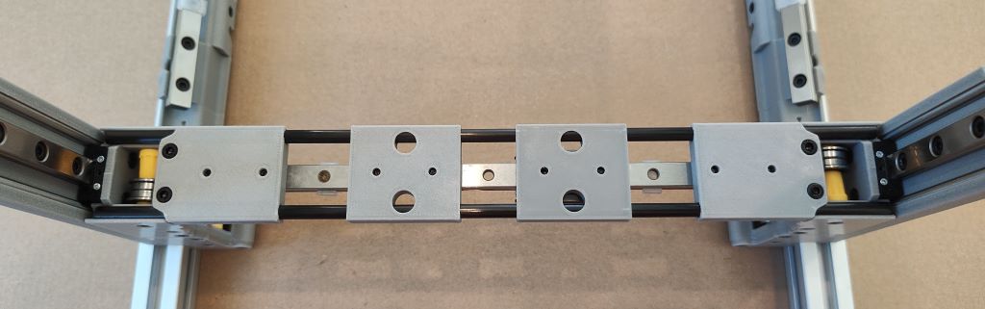
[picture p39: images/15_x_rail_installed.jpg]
  
</p>

> [!Tip]  
> You can now test the gantry motion by hand and ensure it feels smooth

## Rear Z Motor Mount

- Note: Depending on printer tolerance, use a 5mm reamer on all the parts prior to joining them together
- Start with the Z1 motor mount and add the metal 280mm rods
  - Note: Don't forget to sand the mating edges to avoid gaps
- Here is the order top to bottom, you'll put bottom in first:
  - bed_Z1_Rail_Mount_top
  - bed_Z1_Rail_Mount
  - bed_Z1_Rail_Mount_Wire_Manage
  - bed_Z1_Rail_Mount
  - bed_Z1_Rail_Mount

<p align="center">
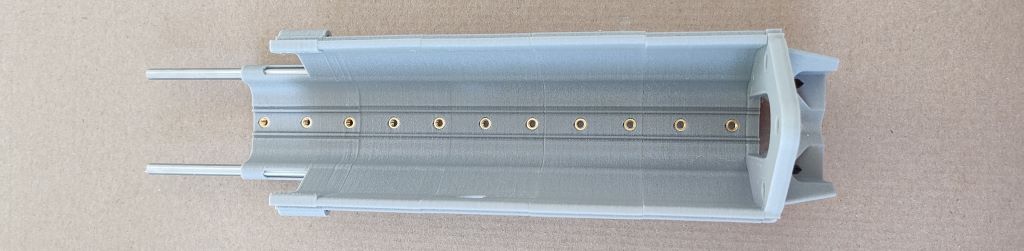
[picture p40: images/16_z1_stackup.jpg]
  
</p>

- Add the Z1 rail using M3x6 (11)

> [!Tip]
> Don't insert the top screw so you can leave the carriage safety clip in place

<p align="center">
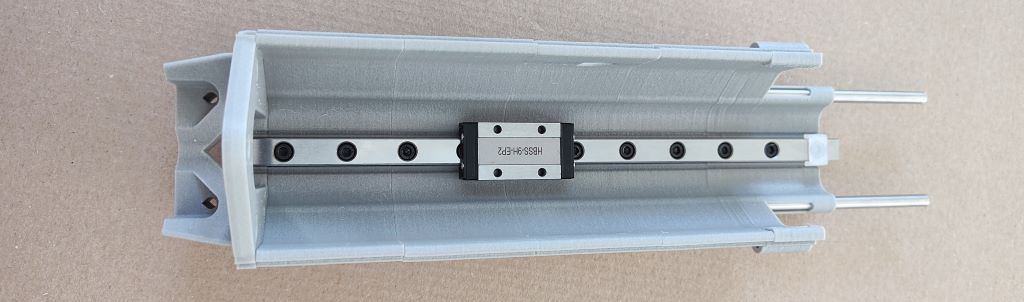
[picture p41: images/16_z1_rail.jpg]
  
</p>

- Use M3x20 (2) for lower screws of the Z1 motor mount, leave loose
- Measure 135mm to center of rear screw from both side extrusions
- Use M3x6 (1) on the back and leave it loose too, you need to slide side to side to finalize the fit
- Install the E3EZ mount to the low voltage ebay mount using M3x8 (2)

<p align="center">
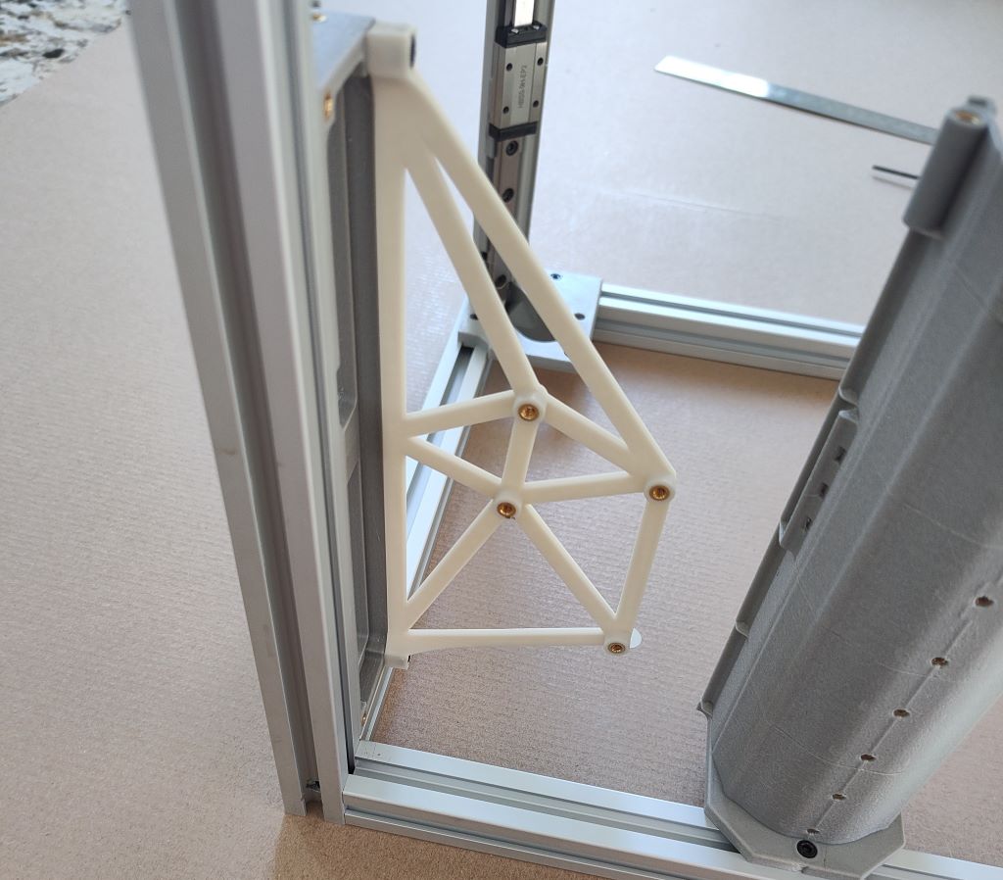
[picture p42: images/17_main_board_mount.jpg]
  
</p>

- Install the mid panels now help get the alignment of Z1
  - Except for the very bottom, the Z Rail Mounts should flex to allow you to pop in the mid panel
    - Start by pushing the panel into the inner flexible side as it should flex enough for you to clear the outer side
  - Note: this assumes your mid panels are accurately cut, otherwise use calipers to get it center

<p align="center">
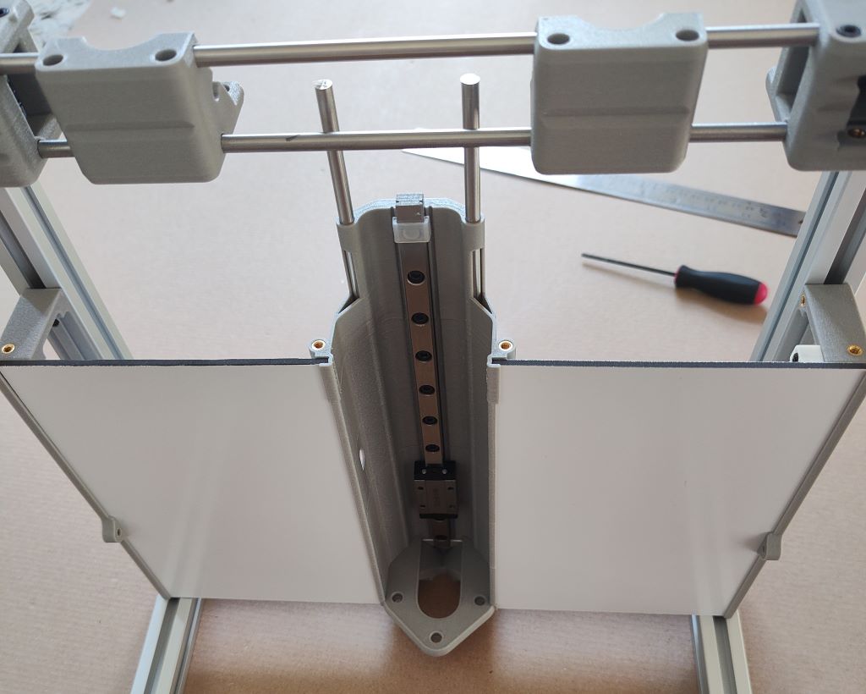
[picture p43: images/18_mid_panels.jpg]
  
</p>

### Rear Z Motor Mount Clamp

- Add the tensioner knobs from behind into the back clamp using M5 nuts (2)
- Add your hex head M4x40 (2) into the back clamp to install the knobs
  - Note: orient the knob so the plastic side is on the outside

<p align="center">
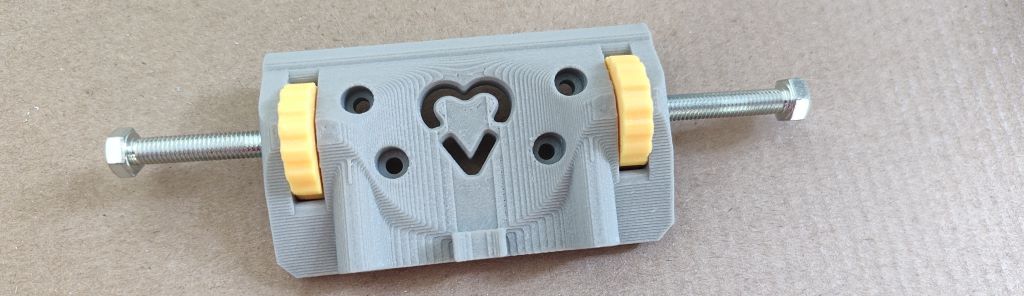
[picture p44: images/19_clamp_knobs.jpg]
  
</p>

- Slide the clamp down over the vertical rods while passing the horizontal rods
  - Note: this part is tricky as you also need to line the hex head screws into motor mounts
- It should seat onto the horizontal rods

<p align="center">
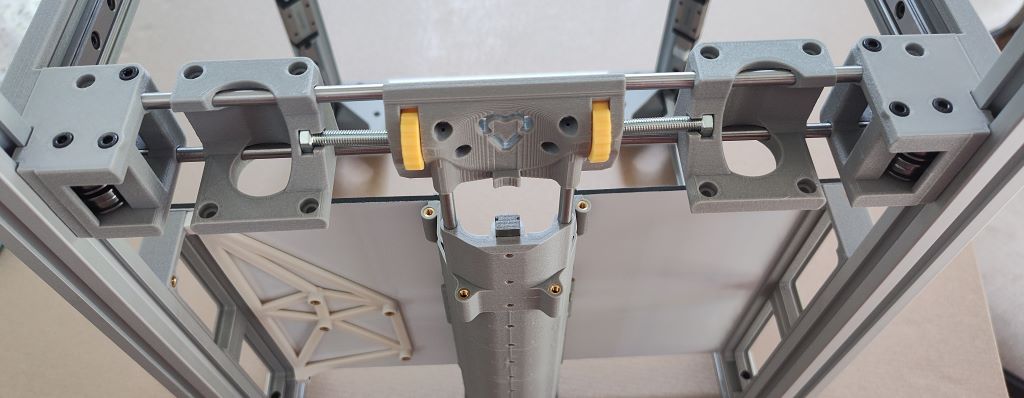
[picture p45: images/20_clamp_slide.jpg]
  
</p>

- Add the front of the clamp using M3x8 (4)
- Before you completely tighten the clamp, check Z1 is centered and square with the frame
- Tighten down the clamp and the Z1 Motor Mount
  - Note: later when we put the ebay tops on, you'll get an idea of well you did with centering

> [!NOTE]  
> At this point the Z1 rail should feel very rigid

## Belts

- Install the pulleys on the A and B motors, use a single bearing stack to help set the proper height
- Add the A and B motors to the rear moto mounts using M3x35 (4) and M3x8 (4)
  - Note: the motor wires should exit towards the side extrusion

<p align="center">
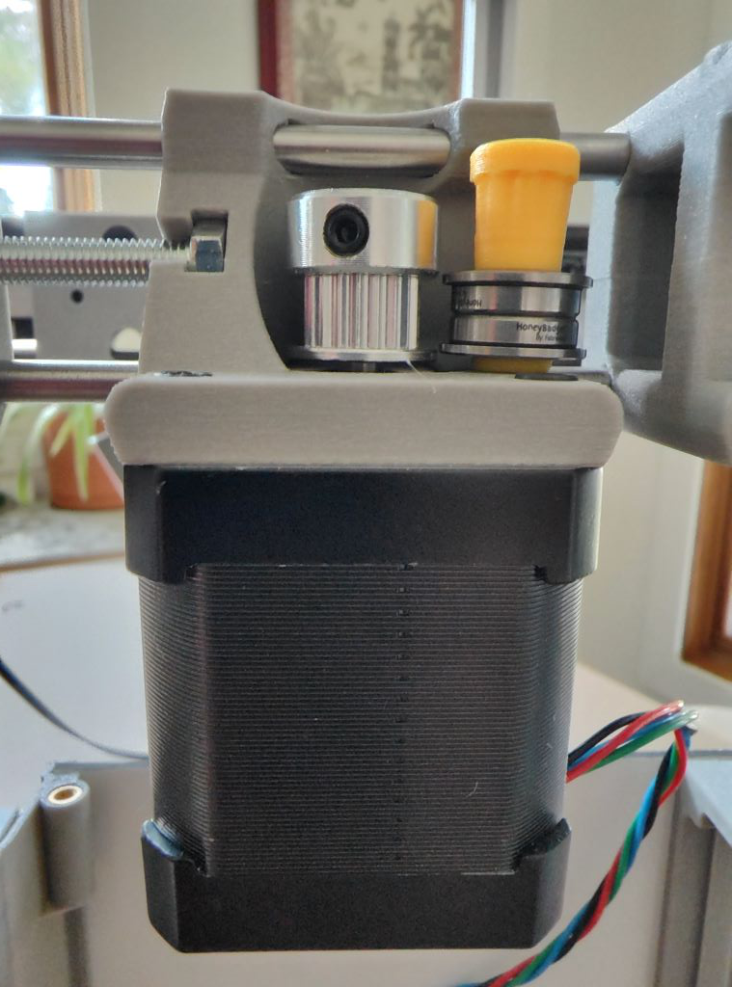
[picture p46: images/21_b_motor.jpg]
  
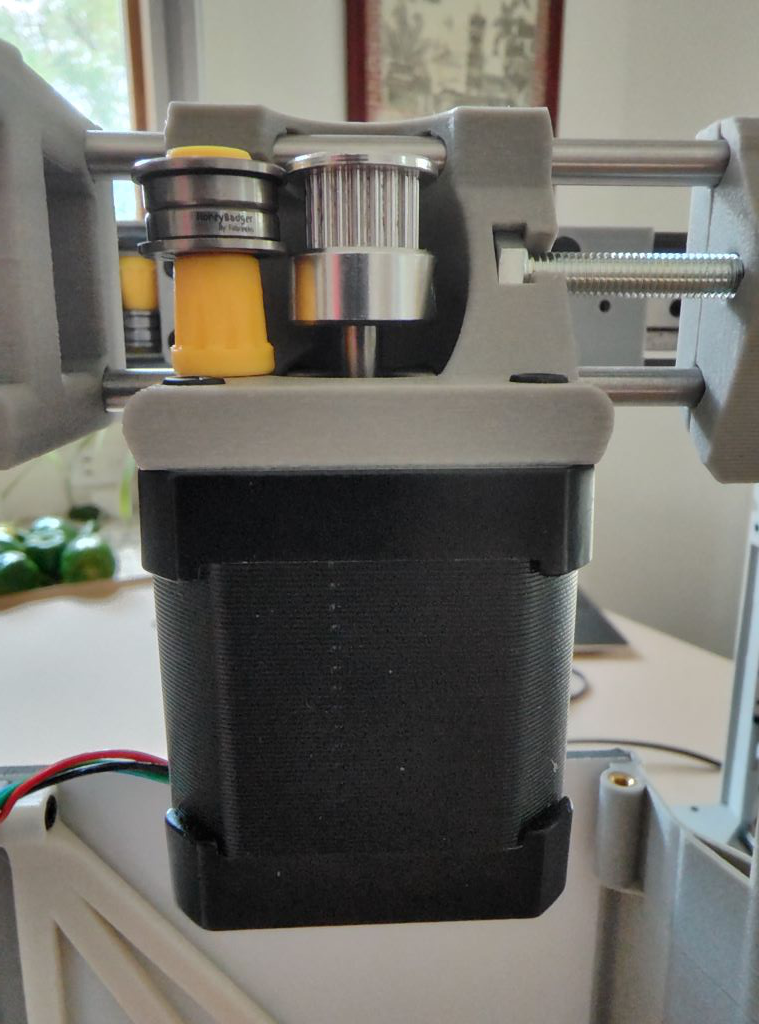
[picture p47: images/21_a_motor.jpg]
  
</p>

- At this point you are still missing some bearings in the rear and the XY joints, this will make routing easier
- Route the belts like any standard Core-XY machine (link to youtube here)
  - Summary: route one side, leaving some slack (try to account for missing bearings)
  - Pull belt out and cut second belt to exact length
  - Put both belts back in

<p align="center">
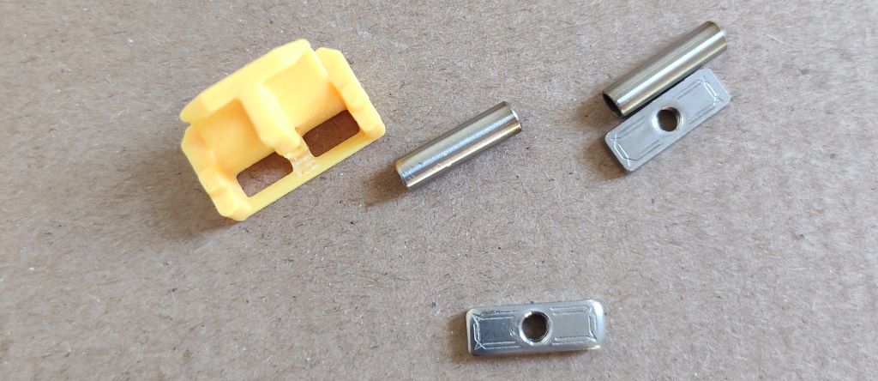
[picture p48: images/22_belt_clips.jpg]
  
</p>

- Add the belts to clips using the 4mm OD and 3mm ID by 15mm long hollow tubes (2)
- Fasten the belts in the clips using M3x10 BHCS (2) and the Makerbeam XL rectangular nuts (2)

<p align="center">
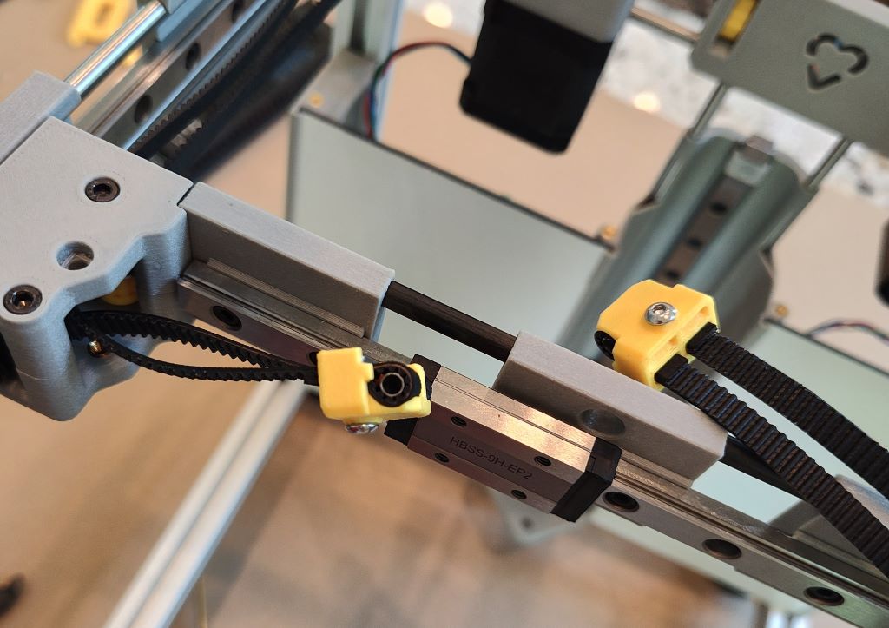
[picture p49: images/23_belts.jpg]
  
</p>

- Add in the missing single stack bearings in the XY joint and front of rear idler

### X-carriage

- Remove the supports from the magnet areas
- Add the 0.5x0.25x0.125" SmCo magnets (10), they should be a tight firm fit with zero wiggle room

> [!NOTE]  
> Make sure the polarity of each set of magnets are attracting together, otherwise you'll get poor hold

- Screw it on the X-carriage using M3x8 (4) screws
  - Note: I find the best print quality with a light tighten, too much and the carriage begins to rock
- Now clip in the belts using the (self-made) pins (2) or M3x35 (2) screws

### Tension belts and tramming

- Start tightening the belts using the knobs in the back
- Periodically check that all the belts are aligning on the bearings properly
- Keep tightening the belts and periodically pluck the back belts to check the tone
- Also, move the gantry as far back as possible
  - If there is an even gap behind both sides of the XY joints, you did a good job!

> [!IMPORTANT]  
> We will dial in the belt tension later using our ShakeTune

## Bed

- Turn the printer upside down
- Add the deck panel using the classic 3mm deck supports
- Mount all three integrated lead-screw motors using M3x6 (9)
- You can route the wires as you wish

<p align="center">
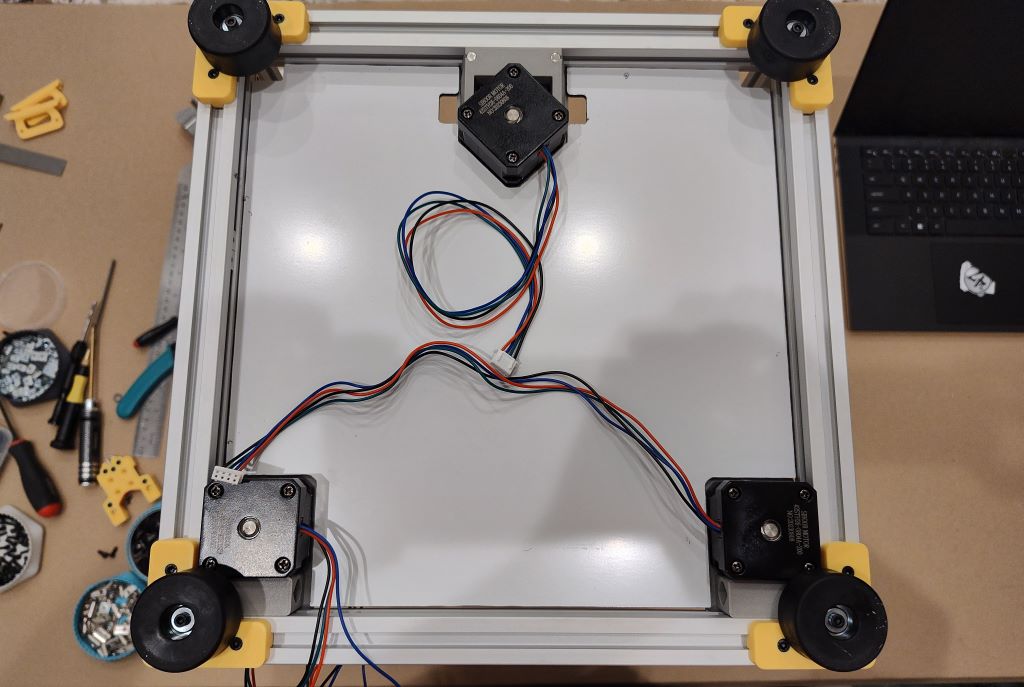
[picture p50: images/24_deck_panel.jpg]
  
</p>

### Z Carriage Mounts

- Add M5x80mm (2) steel rods to mounts using your favorite hammer like tool
  - The rods should end up just barely touching the carriage so don't go too far
- Attach to rail using M3x8 (4)

> [!IMPORTANT]  
> The lead screw should be mostly centered when at the lowest position

- Next add POM nut, twist on and screw down using M3x8 (2)
- Test the up and down movement has no binding

### Kinematic Bed Mounts

- Add the SmCo or High-temp neodymium magnets (6) to carriers, it should be a tight fit so they stay put
- Optional when magnets aren't snug, add a screw to keep the magnets in place
- Slide onto the end of the 80mm steel rods closed end first

> [!IMPORTANT]
> You must use high-temp rated magnets or the bed won't hold-tight after multiple heat-cycles

### Bed Prep

- If your bed doesn't have integrated magnets, add the magnet sheet to the top of the bed
- Add the heater sheet to the underside of the bed
  - Note: pay attention to the routing of the wires doesn't interfere with the rear middle mount
- Use M4x10 (3) to screw on 10mm balls using 2 washers for spacing
- Test fit bed and check that it fits firmly in place with very little movement
  - The magnets should hold the bed firmly, even when upside down

> [!CAUTION]
> Not a problem, but a small amount of movement is normal if you yank on the bed

### Bed wiring

- Add some cable sleeve and route the wires thru the hole near the Z1 lead screw
- Allow enough slack for the bed to move the full range but not so much it catches on anything

## Electronics

> [!CAUTION]
> This build requires mains wiring, only proceed if you are certified to work with high voltages

### PSU

- For the thin PSU mount, add some 3mm thick foam between bracket and deck panel
- Add the PSU mounts using M3x8 for both brackets, tighten the second bracket after a test fit
- Mount the PSU to the bracket using M3x6 (2)

<p align="center">
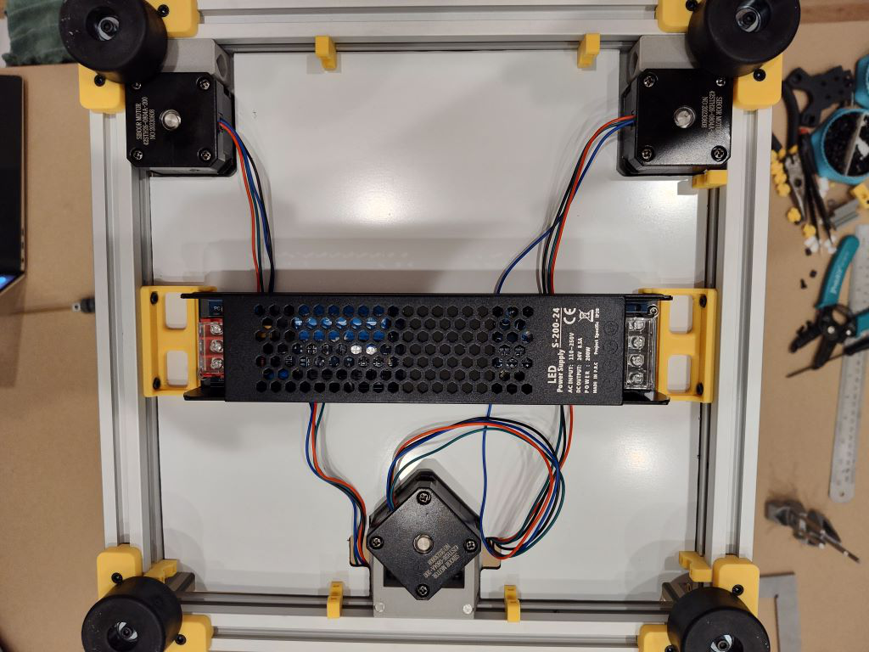
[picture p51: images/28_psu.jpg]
  
</p>

### Main Board

- Insert the E3EZ IO shield into the low voltage ebay mount
- Line the E3EZ ports up and mount using M3x6 (4)

### Mains Inlet

- Pre wire the mains inlet and then insert it into the mount, it should snap in
  - Don't forget to check that a fuse is installed
- Roll-in 2 tnuts and mount the mains inlet using M3x10 (2)
  - Grab the back panel and use for setting the perfect height

> [!CAUTION]
> Proceed to wire up Mini-V using Trident manual

## CAN Toolhead

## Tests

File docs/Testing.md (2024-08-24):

# Z Probe Testing

## Boop with DB 10 samples, multiple random spots
probe accuracy results: maximum -0.622188, minimum -0.625625, range 0.003437, average -0.624094, median -0.624063, standard deviation 0.001078
probe accuracy results: maximum -0.623125, minimum -0.628750, range 0.005625, average -0.625063, median -0.625000, standard deviation 0.001733
probe accuracy results: maximum -0.623750, minimum -0.626875, range 0.003125, average -0.625531, median -0.625625, standard deviation 0.000959
probe accuracy results: maximum -0.628125, minimum -0.633125, range 0.005000, average -0.630219, median -0.630313, standard deviation 0.001370
probe accuracy results: maximum -0.626563, minimum -0.630000, range 0.003437, average -0.628094, median -0.627813, standard deviation 0.000993

## (Redacted) with DB 10 samples
probe accuracy results: maximum -0.649375, minimum -0.663125, range 0.013750, average -0.657625, median -0.658281, standard deviation 0.004638

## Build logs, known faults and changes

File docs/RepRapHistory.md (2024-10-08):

# RepRap History

* __2015 May__ Wilson2 kit from mjrice
* __2021 April__ Wilson2 prints Voron 0.1
* __2021 May__ Voron 0.1 "FireZero" serial 450
* __2021 May__ FireZero prints another Voron 0.1
* __2021 June__ Voron 0.1 "Goldenchild" serial 515
* __2021 August__ FireZero and Goldenchild print Voron Trident
* __2021 October__ Voron Trident "Blue" serial 339
* __2021 December__ Blue partial prints a Voron 2.4 (for makerspace)
* __2022 January__ Blue prints StealthBurner
* __2022 November__ Blue partial prints a Voron 2.4r2 (for friend)
* __2022 November__ Blue prints Voron Tap
* __2023 February__ FireZero and Blue print a Tiny-T 170
* __2023 March__ Tiny-T gets Voron Trident serial 1008
  * Build Log: https://discord.com/channels/825469421346226226/1077302494293667892
* __2023 April__ Blue and Tiny-T prints Mini-V prototype 1
* __2023 April__ Mini-V Y/Z axis prototype shown to Voron team at RMRRF
* __2023 May__ Mini-V prototype first print!
* __2023 July__ FireZero updated to V0.2r1
* __2023 September__ Tiny-T is torn down to rebuild as Mini-V alpha
* __2023 September__ Blue and Mini-V prototype print Mini-V alpha
* __2023 September__ Mini-V alpha shown at ERRF (printopia)
* __2024 April__ Blue and Mini-V alpha prints Mini-V pre-beta parts
* __2024 April__ Mini-V pre-beta shown at RMRRF
* __2024 June__ Beta files released as open source
* __2024 Sept__ BOM, parts, and build guide updated
* __2024 Oct__ Mini-V group build at VICE 2024 in Reno

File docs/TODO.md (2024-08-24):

# Things that still need to be done

docs: better build guide
docs: double check parts count

alpha: bed fuse
alpha: microfit disconnect for bed
alpha: LED lighting
alpha: bottom HV cover
alpha: ebay fan

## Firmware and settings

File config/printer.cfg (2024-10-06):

[include mainsail.cfg]
# [include fluidd.cfg]
[include printer_toolhead_ebb36_revo_g2.cfg]

[mcu]
##	Obtain definition by "ls -l /dev/serial/by-id/" then unplug to verify
#serial: /dev/serial/by-id/usb-Klipper_stm32g0b1xx_4A00290012504B4B38383620-if00
#canbus_uuid: 183fbc1d936f # CM4 EMMC 2G RAM, wifi

[exclude_object]
[gcode_arcs]
resolution: 0.1

[temperature_sensor raspberry_pi]
sensor_type: temperature_host
min_temp: 10
max_temp: 100

[temperature_sensor e3ez]
sensor_type: temperature_mcu
min_temp: 0
max_temp: 100

[printer]
kinematics: corexy
max_velocity: 500  
max_accel: 15000 # we can go up to 20k latest IS results
max_z_velocity: 15 		
max_z_accel: 120
square_corner_velocity: 5.0

[input_shaper]
shaper_type_x: mzv
shaper_freq_x: 46.8 # update for your build
shaper_type_y: mzv
shaper_freq_y: 30.6 # update for your build

#####################################################################
# 	X/Y Stepper Settings
#####################################################################

[stepper_x]
##  B Stepper - Left
##	Connected to MOTOR_0
##  Endstop connected to DIAG_0

step_pin: PA14
dir_pin: !PA10
enable_pin: !PA13
rotation_distance: 40
microsteps: 32
full_steps_per_rotation:200  #set to 400 for 0.9 degree stepper

endstop_pin: tmc5160_stepper_x:virtual_endstop #^PC4
position_endstop: 180
position_min: 0
position_max: 180
homing_speed: 60   #Max 100
homing_retract_dist: 0
homing_positive_dir: true

##	Make sure to update below for your relevant driver (2208 or 2209)
[tmc5160 stepper_x]
cs_pin: PB8
spi_software_miso_pin: PC11
spi_software_mosi_pin: PC12
spi_software_sclk_pin: PC10
diag1_pin: ^!PC4 #PF3 #PC4?
run_current: 1.1
#stealthchop_threshold: 999999
interpolate: false
#driver_SGTHRS: 65 #45 #85 #58 #34
driver_SGT: 3


[stepper_y]
##  A Stepper - Right
step_pin: PC8
dir_pin: !PA15
enable_pin: !PC14

rotation_distance: 40
microsteps: 32
full_steps_per_rotation:200  #set to 400 for 0.9 degree stepper

endstop_pin: tmc5160_stepper_y:virtual_endstop #^PB0
position_endstop: 180
position_min: 0
position_max: 180
homing_speed: 60
homing_retract_dist: 0
homing_positive_dir: true

##	Make sure to update below for your relevant driver (2208 or 2209)
[tmc5160 stepper_y]
cs_pin: PC9
spi_software_miso_pin: PC11
spi_software_mosi_pin: PC12
spi_software_sclk_pin: PC10
diag1_pin: ^!PB0 #^!PF4 #PB0?
run_current: 1.1
#stealthchop_threshold: 999999
interpolate: false
#driver_SGTHRS: 65 #45 #105
driver_SGT: 2

#####################################################################
# 	Z Stepper Settings
#####################################################################

#LDO V0.1 Teflon coated 8x8 leadscrew Z motor
#resistance: 5.5
#inductance: 0.007
#holding_torque: 0.24
#max_current: 1
#steps_per_revolution: 200

#Siboor BOM Voron 0.2 Z integrated leadscrew stepper
#resistance: 5.5
#inductance: 0.0066
#holding_torque: 0.26
#max_current: 1.0
#steps_per_revolution: 200

[stepper_z]
step_pin: PD5
dir_pin: PD6
enable_pin: !PB3
microsteps: 128
rotation_distance: 8
full_steps_per_rotation: 200	#200 for 1.8 degree, 400 for 0.9 degree

endstop_pin: probe:z_virtual_endstop # ^PC6
position_max: 180
position_min: -2.5
homing_speed: 7 # for PZ probe want to go at least medium speed
second_homing_speed: 7
homing_retract_dist: 2


##	Make sure to update below for your relevant driver (2208 or 2209)
[tmc2209 stepper_z]
uart_pin: PD1
run_current: 0.37
interpolate: false
stealthchop_threshold: 999999

##	Z1 Stepper - Rear Z Motor
##	E0 Stepper Socket
[stepper_z1]
step_pin: PD2
dir_pin: PD4
enable_pin: !PD3
microsteps: 128
rotation_distance: 8	
full_steps_per_rotation: 200	#200 for 1.8 degree, 400 for 0.9 degree

##	Make sure to update below for your relevant driver (2208 or 2209)
[tmc2209 stepper_z1]
uart_pin: PD0
run_current: 0.37
interpolate: false
stealthchop_threshold: 999999


##	Z2 Stepper - Right Rear Z Motor
##	E1 Stepper Socket
[stepper_z2]
step_pin: PB7
dir_pin: PB6
enable_pin: !PB4		
microsteps: 128
rotation_distance: 8	
full_steps_per_rotation: 200	#200 for 1.8 degree, 400 for 0.9 degree

[tmc2209 stepper_z2]
uart_pin: PB5
run_current: 0.37
interpolate: false
stealthchop_threshold: 999999


[homing_override]
gcode:
  {% set home_all = 'X' not in params and 'Y' not in params and 'Z' not in params %}

  {% if home_all or 'X' in params %}
    _HOME_X
  {% endif %}
  
  {% if home_all or 'Y' in params %}
    _HOME_Y
  {% endif %}
  
  {% if home_all or 'Z' in params %}
  
    G90
    G1 X93 Y103 F5000
    G28 Z
    G1 Z10
  {% endif %}

#####################################################################
# 	Bed Heater
#####################################################################

[heater_bed]
##	SSR Pin - PA1
##  Thermistor - TB
heater_pin: PB2 
sensor_type: EPCOS 100K B57560G104F
sensor_pin: PA3 
min_temp: 0
max_temp: 120
#control: pid
#pid_kp: 37.715
#pid_ki: 1.890
#pid_kd: 188.105

#6/1/2023 70% 300w bed pid_Kp=37.715 pid_Ki=1.890 pid_Kd=188.105
#31.305 pid_Ki=2.485 pid_Kd=98.611


#####################################################################
#   Probe
#####################################################################
[probe]
pin: ^can0:PB6
x_offset: 0
y_offset: 0
#z_offset: -1.390
speed: 7
samples: 2
sample_retract_dist: 3
lift_speed: 10
samples_result: median
samples_tolerance: 0.015
samples_tolerance_retries: 5
activate_gcode:
    {% set PROBE_TEMP = 155 %}
    {% set MAX_TEMP = PROBE_TEMP + 5 %}
    {% set ACTUAL_TEMP = printer.extruder.temperature %}
    {% set TARGET_TEMP = printer.extruder.target %}

    {% if TARGET_TEMP > PROBE_TEMP %}
        { action_respond_info('Extruder temperature target of %.1fC is too high, lowering to %.1fC' % (TARGET_TEMP, PROBE_TEMP)) }
        M109 S{ PROBE_TEMP }
    {% else %}
        # Temperature target is already low enough, but nozzle may still be too hot.
        {% if ACTUAL_TEMP > MAX_TEMP %}
            { action_respond_info('Extruder temperature %.1fC is still too high, waiting until below %.1fC' % (ACTUAL_TEMP, MAX_TEMP)) }
            TEMPERATURE_WAIT SENSOR=extruder MAXIMUM={ MAX_TEMP }
        {% endif %}
    {% endif %}
    G4 P200 ;Wait 200ms
    SET_TMC_CURRENT STEPPER=stepper_z CURRENT=0.27
    SET_TMC_CURRENT STEPPER=stepper_z1 CURRENT=0.27
    SET_TMC_CURRENT STEPPER=stepper_z2 CURRENT=0.27
    SET_TMC_CURRENT STEPPER=stepper_z3 CURRENT=0.27
deactivate_gcode:
    {% set run_current = printer.configfile.config['tmc2209 stepper_z'].run_current | float %}
    SET_TMC_CURRENT STEPPER=stepper_z CURRENT={run_current}
    SET_TMC_CURRENT STEPPER=stepper_z1 CURRENT={run_current}
    SET_TMC_CURRENT STEPPER=stepper_z2 CURRENT={run_current}
    SET_TMC_CURRENT STEPPER=stepper_z3 CURRENT={run_current}

#####################################################################
# 	Fan Control
#####################################################################
#PA8 Fan0
#PB15 Fan1
#PB14 Fan2

[fan_generic ebay_fan]
pin: PA8 # PB15 or PB14
kick_start_time: 2.0
max_power: 1.0
off_below: 0.50

#[led left_lights]
#white_pin: PB11
#initial_WHITE: 0.5

#[led right_lights]
#white_pin: PB10
#initial_WHITE: 0.5

[idle_timeout]
timeout: 3000 # 1800


#####################################################################
# 	Displays
#####################################################################

[board_pins]
aliases:
    # EXP1 header
    EXP1_1=PC1, EXP1_3=PC3, EXP1_5=PC0, EXP1_7=PA2, EXP1_9=<GND>,
    EXP1_2=PC2,  EXP1_4=<RST>, EXP1_6=PA0, EXP1_8=PA1, EXP1_10=<5V>

    

#####################################################################
# 	Macros
#####################################################################
[z_tilt]
z_positions: # bed pivot points, you can easily check since they are directly above screw holes
	7, 48
	93, 177
	177, 48
points: # nozzle probe points
	17, 48
	93, 167
	167, 48
speed: 200
horizontal_move_z: 3
retries: 4
retry_tolerance: 0.0075



[bed_mesh]
speed: 300
mesh_min: 15,15
mesh_max: 165,165
probe_count: 5,5
# relative_reference_index: 12

[gcode_macro LOAD_FILAMENT]
gcode:
    G1 E50 F240
    G1 E50 F240
    G1 E50 F240
    G1 E50 F240

[gcode_macro Z_TILT]
gcode:
    Z_TILT_ADJUST

[gcode_macro PURGE_LINE]
gcode:
    M117 Purging filament...
    G92 E0;
    G90
    G0 X5 Y5 F6000
    G0 Z0.4
    G91
    G1 X60 E10 F600;
    G1 Y1
    G1 X-60 E10 F600;
    G92 E0;
    G90

[gcode_macro PRINT_START]
gcode:
    SET_FAN_SPEED FAN=ebay_fan SPEED=0.31

    M117 Homing...
    G28 Y0 X0 Z0
    Z_TILT_ADJUST
    G28 Z
    
    M117 Bed Mesh Calibration...
    BED_MESH_CALIBRATE ADAPTIVE=1 ADAPTIVE_MARGIN=5
    
    M117 Recovering temp...
    {% set EXT_TEMP = params.EXTRUDER|int %}
    M109 S{ EXT_TEMP }
    
    PURGE_LINE
    
    G1 Z15.0 F600 ;move the platform down 15mm
    G1 X82 Y82 F3000
    G92 E0 ;zero the extruded length again
    G1 F9000
    M117 Printing...
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

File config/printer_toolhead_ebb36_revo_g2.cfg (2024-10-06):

## BOARD PINS
[board_pins EBB36_G0B1_v1.2] 
mcu: can0
aliases:
aliases_step:
    EXT_EN=PD2,EXT_STEP=PD0,EXT_DIR=PD1,EXT_UART=PA15
aliases_limitsw: # these are preferred for endstops (including klicky)
    LIMIT_1=PB7,LIMIT_2=PB5,LIMIT_3=PB6
aliases_bltouch: # these are the dupont connectors for bltouch
    PROBE_1=PB9,PROBE_2=PB8
aliases_fans:
    FAN0=PA1,FAN1=PA0
aliases_thermistors:
    TH0=PA3,PT100_CS=PA4,PT100_SCLK=PA5,PT100_MISO=PA6,PT100_MOSI=PA7
aliases_heaters:
    HE0=PB13
aliases_rgb:
    RGBLED=PD3
aliases_adxl:
    ADXL_CS=PB12,ADXL_SCLK=PB10,ADXL_MISO=PB2,ADXL_MOSI=PB11
aliases_i2c:
    AUX0=PB3,AUX1=PB4

## can0
[mcu can0]
# run the following command to locate the uuid >   ~/klippy-env/bin/python ~/klipper/scripts/canbus_query.py can0
#canbus_uuid: 554e72f68a49 
#canbus_uuid: be31d2e5af35
canbus_uuid: 73e4cbe1663b

# onboard temp
[temperature_sensor EBB36]
sensor_type: temperature_mcu
sensor_mcu: can0

[adxl345]
cs_pin: can0:ADXL_CS
spi_software_sclk_pin: can0:ADXL_SCLK
spi_software_mosi_pin: can0:ADXL_MOSI
spi_software_miso_pin: can0:ADXL_MISO
axes_map: x,y,z

#[temperature_sensor PT100]
#sensor_type: MAX31865
#sensor_pin: can0:PT100_CS
#spi_bus: spi1
#min_temp: -50
#max_temp: 350
#rtd_reference_r: 430

[heater_fan hotend_fan]
pin: can0:FAN0
max_power: 1.0
kick_start_time: 0.5
heater: extruder
heater_temp: 50.0
#fan_speed: 0.5

## PART COOLING
[fan]
pin: can0:FAN1
kick_start_time: 0.25
cycle_time: 0.15
off_below: 0.10

## EXTRUDER 
[extruder]
step_pin: can0:EXT_STEP
dir_pin: can0:EXT_DIR
enable_pin: !can0:EXT_EN
rotation_distance: 47.088
gear_ratio: 9:1
microsteps: 16

max_extrude_cross_section: 30
max_extrude_only_distance: 1400.0
max_extrude_only_velocity: 75.0
max_extrude_only_accel: 1500
nozzle_diameter: 0.600
filament_diameter: 1.750
heater_pin: can0:HE0

sensor_pin: can0:TH0
sensor_type: ATC Semitec 104NT-4-R025H42G #ATC Semitec 104GT-2  # this is the default for the Revo heater
#pullup_resistor: 2200             # this is the default for the Revo heater

#sensor_type:MAX31865
#sensor_pin: can0:PT100_CS
#spi_bus: spi1
#rtd_nominal_r: 100
#rtd_reference_r: 430
#rtd_num_of_wires: 2

control: pid
pid_Kp: 36.050
pid_Ki: 4.292
pid_Kd: 75.705
min_temp: -50
max_temp: 310

pressure_advance: 0.035 #fusion abs #0.026 # 0.0275

#8/24/2023 pid_Kp=36.050 pid_Ki=4.292 pid_Kd=75.705
#6/1/2023 pid_Kp=34.133 pid_Ki=4.214 pid_Kd=69.119
#5/22/2023 pid_Kp=35.153 pid_Ki=4.507 pid_Kd=68.547
#5/21/2023 pid_Kp=30.814 pid_Ki=4.109 pid_Kd=57.777
#pid_Kp=23.466 pid_Ki=1.435 pid_Kd=95.918
#pid_Kp=23.929 pid_Ki=1.491 pid_Kd=96.013

## EXTRUDER MOTOR
[tmc2209 extruder]
uart_pin: can0:EXT_UART
run_current: 0.6
sense_resistor: 0.110
stealthchop_threshold: 0

[resonance_tester]
accel_chip: adxl345
probe_points: 90,90,90

## RGB
#[neopixel my_neopixel]
#pin: can0:RGBLED
#chain_count: 12
#color_order: GRB
#initial_RED: 0.0
#initial_GREEN: 0.0
#initial_BLUE: 0.0

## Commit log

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2023-06-28 Add prototype images
    [printer.cfg, printer_toolhead_ebb36_mini_SB.cfg, printer_toolhead_ebb36_revo_HGX.cfg]
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2024-04-18 Parts and docs updates
    [[a]_bed_Kinematic_Mount_Cover_x3.stl, bed_Front_Z_Rail_Mount_x8.stl, bed_Kinematic_Mount_SaCo_x3.stl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]
2024-06-16 Pre-beta backup
    [Deck_Panel_ACM.step, [a]_bed_Kinematic_Mount_Cover_x3.stl, bed_Front_Z_Rail_Mount_x8.stl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]
2024-08-24 Update parts and docs
    [bed_Front_Z_Rail_Mount_Panel_x2.stl, bed_Mag_Kinematic Mount_x3.stl, bed_Z1_Rail_Mount_Top_x1.stl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]
2024-08-26 Add missing parts (more coming soon)
    [bed_Front_Z_Rail_Mount_x8.stl, bed_Mag_Kinematic_Mount_x3.stl, panels_Clip_Mount_1Scew_x8.stl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]
2024-08-26 Add AB motor mounts
    [gantry_A_Motor_Mount_Top_x1.stl, gantry_A_Motor_Mount_x1.stl, gantry_B_Motor_Mount_Bottom_x1.stl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]
2024-08-30 Add Y rail mount
    [gantry_Y_Rail_Mount_x4.stl]
2024-08-30 Y rail mount
    [gantry_Y_Rail_Mount_x4.stl]
2024-08-31 Front idlers
    [gantry_Front_Idler_Bot_Left_x1.stl, gantry_Front_Idler_Bot_Right_x1.stl, gantry_Front_Idler_Top_Left_x1.stl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]
2024-08-31 Front idler
    [gantry_Front_Idler_Bot_Left_x1.stl, gantry_Front_Idler_Bot_Right_x1.stl, gantry_Front_Idler_Top_Left_x1.stl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]
2024-08-31 Update gantry
    [gantry_A_Motor_Mount_Bot_x1.stl, gantry_A_Motor_Mount_Top_x1.stl, gantry_B_Motor_Mount_Bot_x1.stl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]
2024-08-31 Gantry and panels update
    [gantry_XY_Joint_Left_Bot_x1.stl, gantry_XY_Joint_Left_Top_x1.stl, gantry_XY_Joint_Right_Bot_x1.stl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]
2024-09-01 More parts
    [bed_Z1_Top_Tensioner_Clamp_Back_x1.stl, bed_Z1_Top_Tensioner_Clamp_Front_x1.stl, bed_[a]_Z1_Rear_Top_Tensioner_Knob_x3.stl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]
2024-09-01 XY joint update
    [bed_Z1_Rear_Motor_Mount_x1.stl, gantry_XY_Joint_Left_Bot_x1.stl, gantry_XY_Joint_Left_Top_x1.stl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]
2024-09-01 Front Z motor mounts
    [bed_Z0_Motor_Mount_x1.stl, bed_Z1_Motor_Mount_x1.stl]
2024-09-01 Missing parts
    [bed_Z1_Motor_Mount_x1.stl, bed_Z1_Rear_Motor_Mount_x1.stl, bed_Z1_Top_Tensioner_Clamp_Front_x1.stl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]
2024-09-01 New panel mount layout
    [bed_Front_Z_Rail_Mount_Lower_Left_Panel_x1.stl, bed_Front_Z_Rail_Mount_Lower_Right_Panel_x1.stl, bed_Front_Z_Rail_Mount_x6.stl]
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2024-09-10 Tiny tweaks to bed Z1 parts
    [bed_Front_Z_Rail_Panel_A_Mount_x2.stl, bed_Front_Z_Rail_Panel_B_Mount_x2.stl, bed_Z1_Rail_Mount_Top_x1.stl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]
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2024-09-23 MIC-6 bed step file
    [185_Mini-V_MIC-6_Bed_v3.step, bed_Z1_Motor_Mount_x1.stl, gantry_X_Carriage_Magnetic_x1.stl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]
2024-09-26 Revo PZ Magnetic Toolhead
    [ebay_Mains_Inlet_Mount_x1.stl, gantry_X_Carriage_Magnetic_x1.stl, gantry_[a]_Belt_Clip_x2.stl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]
2024-09-26 Fix clip fit with mag x-carriage
    [gantry_X_Carriage_Magnetic_x1.stl]
2024-09-26 Updated cowl w/ logo
    [toolhead_Yavoth_Revo_PZ_Magnetic_Cowl_x1.stl]
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2024-09-28 Mains inlet tweek for safety
    [ebay_Mains_Inlet_Mount_x1.stl, ebay_[a]_High_Voltage_Mesh_x1.stl, ebay_[a]_Low_Voltage_Mesh_x1.stl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]
2024-09-28 Fix clip orientation
    [panels_Clip_x31.stl]
2024-09-28 Add missing accent parts
    [ebay_Mains_Inlet_Mount_x1.stl, ebay_[a]_Foot_Mount_x4.stl, panels_[a]_Door_Handle_x1.stl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]
2024-09-29 Add panel step files
    [Back_Panel_ACM_or_Clear.step, Side_Panels_Clear.step, Top_Panel_Clear.step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]
2024-09-29 Add panels and front door hinge
    [Back_Panel_ACM_or_Clear_v3.step, Deck_Panel_ACM_v1.step, Deck_Panel_ACM_v4.step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]
2024-09-30 Fix top tensioner bug
    [bed_Z1_Top_Tensioner_Clamp_Back_x1.stl, bed_Z1_Top_Tensioner_Clamp_Front_x1.stl, gantry_[a]_Bearing_Stack_Full_x2_high_tolerance.stl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]
2024-09-30 Fix clamp orientation
    [bed_Z1_Top_Tensioner_Clamp_Back_x1.stl, bed_Z1_Top_Tensioner_Clamp_Front_x1.stl]
2024-09-30 Rename E3EZ IO Shield
    [ebay_[a]_E3EZ_IO_Shield_x1.stl]
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2024-10-01 Fix carriage rub on some MGN9H rails
    [gantry_Y_Rail_Mount_x4.stl]
2024-10-01 Tweak Y Rail Mount based on Pnewb feedback
    [bed_[a]_Z1_Top_Tensioner_Knob_x2.stl, gantry_Y_Rail_Mount_x4.stl, panels_[a]_Top_Latch_Mount_x4.3mf]
2024-10-01 Add taller feet for taller Z motors
    [ebay_[a]_Foot_Mount_(LDO)_x4.stl, ebay_[a]_Foot_Mount_(taller)_x4.stl]
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2024-10-02 Build guide image updates
    [bed_Front_Z_Rail_Mount_x4.stl]
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2024-10-02 Fix too tight mount on X carriage
    [gantry_X_Carriage_Magnetic_x1.stl]
2024-10-03 New kinematic bed mounts & PSU mount
    [bed_[a]_Kinematic_Bed_Mount_SaCo_Small_x3.stl, ebay_[a]_PSU_LED_Mount_x2.stl]
2024-10-04 Update build guide, last few missing parts
    [bed_Z0_Motor_Mount_Front_x1.stl, bed_Z2_Motor_Mount_Front_x1.stl, bed_[a]_Kinematic_Bed_Mount_Neo_SH_Large_x3.stl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]
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2024-10-08 Fix typos, update magnet docs
    [bed_[a]_Kinematic_Bed_Mount_SmCo_Small_x3.stl]
2024-10-15 Fix tiny errors in two parts
    [gantry_XY_Joint_Rod_Rail_Backer_x2.stl, gantry_Y_Rail_Mount_x4.stl]
2024-10-16 Fix panel mount clip alignment
    [panels_Clip_Dual_Mount_Wire_Slot_Left_x1.stl, panels_Clip_Dual_Mount_Wire_Slot_Right_x1.stl, panels_Clip_Dual_Mount_x2.stl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]
2024-10-17 Tweak all clips from 5.5mm to 5mm
    [panels_Clip_Door_Hinge_Latch_Left_x1.stl, panels_Clip_Door_Hinge_Latch_Right_x1.stl, panels_Clip_Dual_Mount_Wire_Slot_Left_x1.stl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]
2024-10-21 Updated panel mount clips
    [bed_Front_Z_Rail_Panel_A_Mount_x2.stl, bed_Front_Z_Rail_Panel_B_Mount_x2.stl, bed_Z1_Rail_Mount_Top_x1.stl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]
2024-10-25 Update clips 5.5 to 5mm
    [panels_Clip_LED_Stick_A_x2.stl, panels_Clip_LED_Stick_B_x2.stl]
2024-10-28 Initial support for 16T GT2 toothed idler
    [gantry_Front_Idler_Bot_Right_x1.stl, gantry_Front_Idler_Left_Bot_x1.stl, gantry_Front_Idler_Left_Top_x1.stl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]
2024-11-07 Update clamp and some panel parts
    [bed_Z1_Top_Tensioner_Clamp_Back_x1.stl, bed_Z1_Top_Tensioner_Clamp_Front_x1.stl, panels_Clip_40mm_x6.stl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]
2024-11-09 Front door hinge tweaks
    [panels_Front_Door_Hinge_Lower_Edge_Left_x1.stl, panels_Front_Door_Hinge_Lower_Edge_Right_x1.stl, panels_Front_Door_Hinge_Lower_Mid_Left_x1.stl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]
2024-11-11 Add rear panel bottom mount
    [panels_Rear_Panel_Bottom_Mount_Left_x1.stl, panels_Rear_Panel_Bottom_Mount_Right_x1.stl]
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2024-11-27 New magnetic side panel clips
    [bed_Front_Z_Rail_Mount_Left_Bot_x1.stl, bed_Front_Z_Rail_Mount_Left_Top_x1.stl, bed_Front_Z_Rail_Mount_Right_Bot_x1.stl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]
2024-12-21 Organize new upper clips
    [bed_Front_Z_Rail_Mount_Right_Top_x1.stl, bed_Front_Z_Rail_Mount_Tall_x1.stl, bed_Front_Z_Rail_Mount_x4.stl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]
2024-12-26 ebay low voltage old?
    [bed_Z1_Rail_Mount_Bot_x1.stl, bed_Z1_Rail_Mount_Top_x1.stl, ebay_Low_Voltage_Side_x1.stl]
